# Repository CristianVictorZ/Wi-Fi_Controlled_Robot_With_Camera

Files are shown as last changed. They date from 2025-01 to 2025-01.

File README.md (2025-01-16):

# Wi-Fi Controlled Robot With Camera

## Introduction

  The project is a spider with 4 legs controlled through Wi-Fi. It is equiped with a camera that will transmit the images it records to the app that controls it.

## Description

  The spider will use an ESP32 microcontroller for its access to Wi-Fi. The ESP32 will be connected through I2C to a Camera Module with a FIFO buffer and through serial to another microcontroller, the ESP8266. The ESP8266 will be connected through I2C to a servo motor driver and a gyroscope. The robot will be controlled through an app to which it will transmit the images the camera records. For its power source, 2 18500 Li-ion Batteries will be used. The batteries together supply 7.4V and 4800mAh. As 7.4V is to high for the Servo Driver, a Voltage Step Down Module will be used to reduce it to 5V. A switch is placed between the Batteries and the Voltage Step Down Module to turn off the robot when not in use.
  Each of its legs will have 2 Servo Motors: one at the base rotating on the Z axis, and one rotating on the X axis.
  The body and the legs of the robot are 3D printed.

## Hardware Design

### Block Diagram

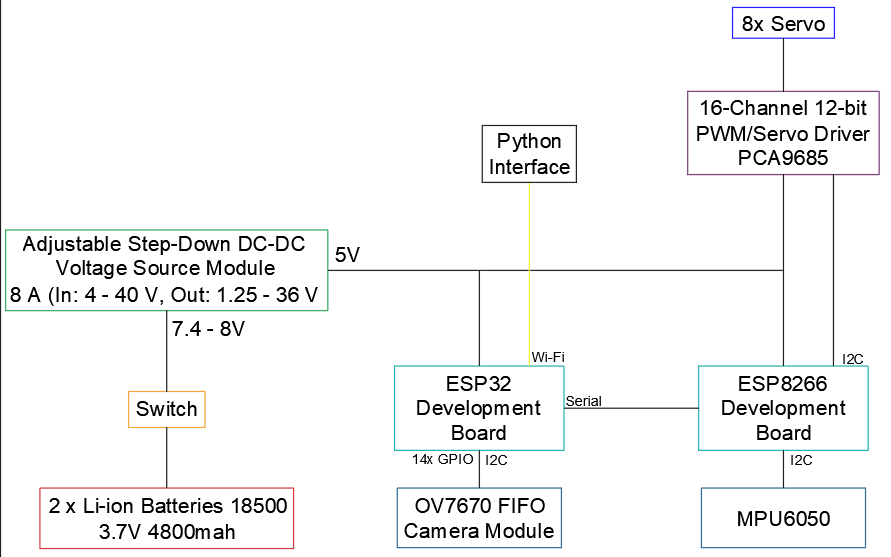
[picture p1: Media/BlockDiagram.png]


### Electric Diagram

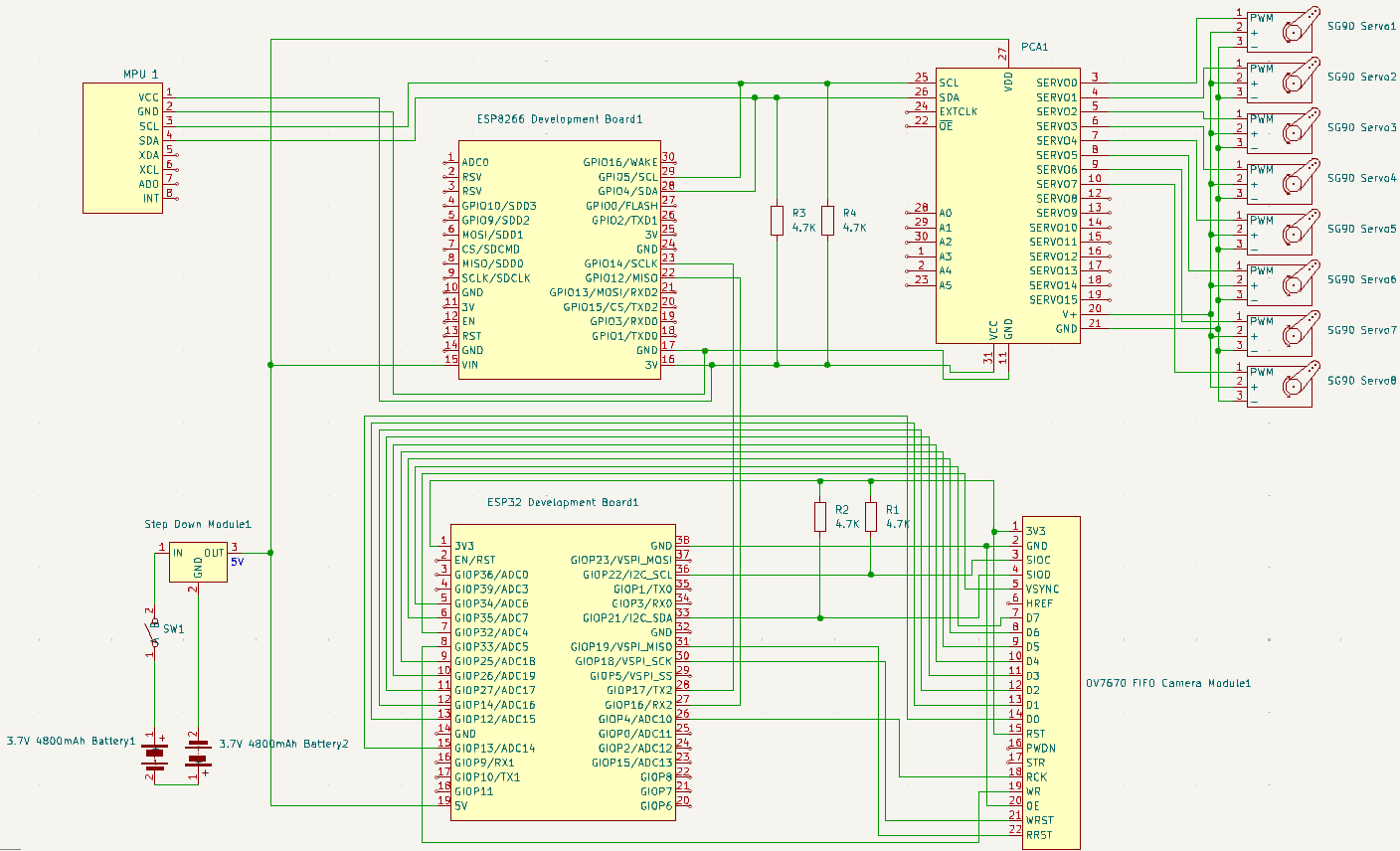
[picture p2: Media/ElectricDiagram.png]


### Components

| Component | Count | Place of Aquisition | Datasheet |
|---|---|---|--- |
| ESP32 Development Board | 1 | Optiums Digital | https://www.espressif.com/sites/default/files/documentation/esp32_datasheet_en.pdf |
| ESP8266 Development Board | 1 | Optimus Digital | https://www.espressif.com/sites/default/files/documentation/esp8266-technical_reference_en.pdf |
| PCA9685 Servo Driver | 1 | Optimus Digital | https://cdn-shop.adafruit.com/datasheets/PCA9685.pdf |
| SG90 Servo Motor | 8 | Optimus Digital | http://www.ee.ic.ac.uk/pcheung/teaching/DE1_EE/stores/sg90_datasheet.pdf |
| OV7670 + AL422B FIFO Camera Module | 1 | Optimus Digital | https://www.haoyuelectronics.com/Attachment/OV7670%20+%20AL422B%28FIFO%29%20Camera%20Module%28V2.0%29/OV7670%20Implementation%20Guide%20%28V1.0%29.pdf|
| Voltage Step Down Module (8A; In: 4-40V, Out: 1.25-36V) | 1 | Optimus Digital | - |
| Battery Support 2x 18500 | 1 | Optimus Digital | - |
| 18500 Li-Ion Battery 3.7V 4800mAh | 2 | - | - |
| 4.7K Resistor | 4 | - | - |
| Wires | - | Optimus Digital | - |

### 3D Model

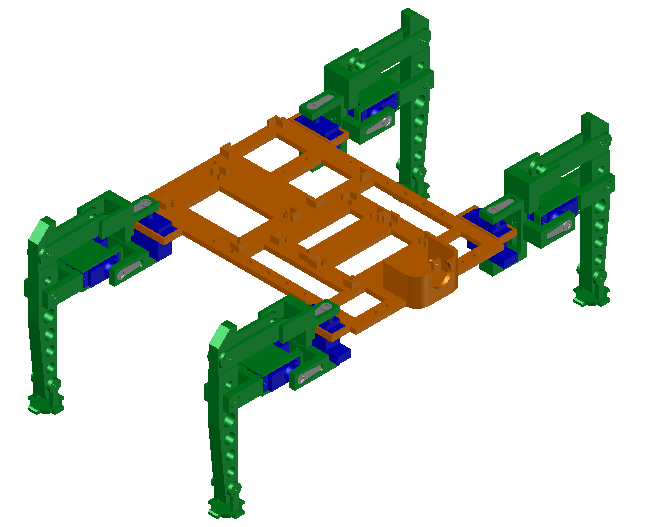
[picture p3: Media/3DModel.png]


### Implementation

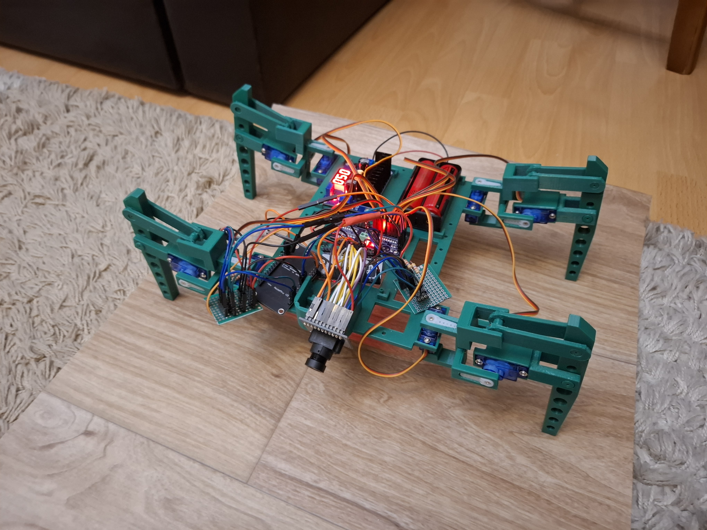
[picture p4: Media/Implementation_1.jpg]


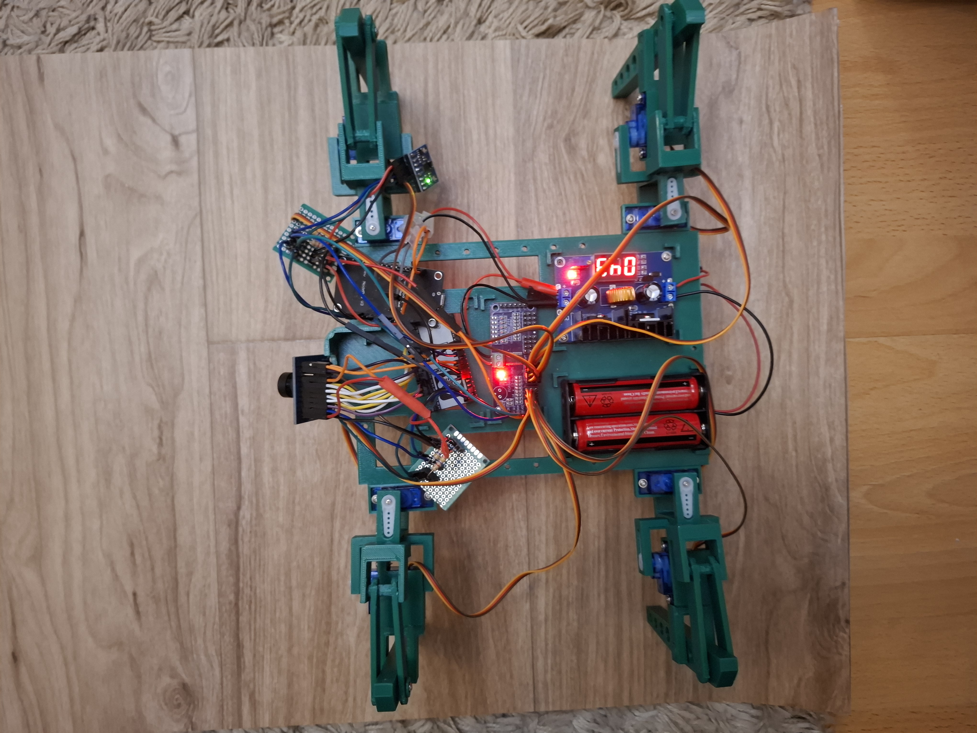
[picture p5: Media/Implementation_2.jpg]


## Software Design

  The software of the robot can be broken into 2 parts: the control of the robot and the interface. The control can also be broken into 3 parts: the wi-fi control, the camera control and the movement control.

  ### Wi-Fi Control

  Wi-Fi is handled by the Core1 on the ESP32. The ESP32 functions as an access point that a client can connect to. It will check in the loop function wether or not a client has connected. Once a client connects, it will begin checking for received messages. When a message is received, it will read the first byte of the message, which identifies the type of message received. The types of messages it can receive from the client are: control update, acknowledge and disconnect. If the message was a control update, it will read the next 3 bytes which represent the 3 variables that coordonate the behaviour of the entire robot: CAMERA_CONTROL1, CAMERA_CONTROL2, MOVEMENT_CONTROL. It will then update its control variables with the ones received and send a confirmation to the client. If the message was an acknowledge, then it means the client confirmed data sent by the Core0, so it will update the variable 'acknowledeAvailable' to let Core0 know it can send the next data set. If the message was a disconnect, the ESP disconnect from the client and resets it's control variables.

  Besides controlling the Wi-Fi, Core1 also handles communication with the ESP8266 through Serial2. When MOVEMENT_CONTROL is updated, it will send through Serial2 the updated variable to the ESP8266.

  ### Camera Control

  The camera is handled by the Core0 on the ESP32. The OV7670 Camera is initialised in the setup function of the program, but afterwards it is controlled only by Core0. It will continuasly check CAMERA_CONTROL1 and CAMERA_CONTROL2 to see if the settings of the camera have to be reconfigured, and if the camera has been enabled. If the camera is enabled it will begin to read and send the frame.

  As stated previosly, the camera has a FIFO memory attached to it. As such, when the camera captures a frame, it will be stored entirely on the FIFO memory, so it is not necessary to store it in a variable. The camera can take pictures in 3 resolutions: 320x240, 160x120, 80x60. Pictures are taken in the RGB565 format: a pixel takes up only 2 bytes, with the first 5 bits being red, the next 6 being green, and the last 5 blue. For easier transmission through Wi-Fi, a variable will store 1024 bytes (+ 1 byte in the begging to indicate the begginig of the set), which will then be sent. Before sending another set of bytes, Core1 will wait for the variable 'acknowledgeAvailable' to indicate that the byte set has been received by the client. If a short amount of time passes with no acknowledge, then the image will no longer be read, and the camera will deactivate.

  ### Other notes regarding the ESP32

  Since both cores can send data thorugh Wi-Fi, the ESP32 uses the mutex library to lock the function for sending data when one of the cores is using it.

  ### Movement Control

  Movement is handled by the ESP8266. It stores 4 matrices that hold the values for each of the 8 motors during a certain movement and an array for idle, that stores the default value for the motors. The 5 matrices are for: forward, backwartd, turn left, turn right. It also stores an array for error values, since the motors are not centered (my bad). It uses the Adafruit Servo Driver to interract with the PCA9685. It will check in its loop for updates to the MOVEMENT_CONTROL variable thorugh a serial port created using the Software Serial library. Depending on its value it will begin one of the movements described. The ESP8266 is also connected to a MPU6050 Accelerometer used to determine the tilt of the body. Based on this, if configured to do so from the interface, it can calculate the error of the servomotrs, and, using a pid, adjust itself so that the body is parallel to the ground.

  ### Interface

  The interface through which the robot is controlled has been realized in Python. The interface uses 3 threads to manage the tasks requiered for controlling the robot.

  The first thread is for the Wi-Fi Control. It uses 2 global variables: a stack for data it receives on Wi-Fi and a stack for data it has to send thorugh Wi-Fi. When it reads data from the Wi-Fi, it is stored in a buffer that can contrain multiple messages appended to each other. Similarly to the ESP32, it checks received data by looking at the first byte of the message. A message can either be a confirmation, or a set of bytes from an image. If it's the former, then the thread will remember it in a variable, and it will remove one byte from the data received buffer. If it's the latter, it will copy the set of bytes to the received data stack and remove 1025 from the data received buffer. If it is neither, then it will begin discarding bytes until it finds a byte that corresponds to one of the previosly mentioned cases. It will repeat this until the buffer is empty. If either thread needs to send data, it will store in the data to send stack, which will be continuasly checked by this thread. After sending a message it will wait for confirmation from the ESP.

  The second thread handles image processing. It receives from the previous thread a set of bytes through the received data stack. It the processes those bytes: it converts them from RGB565 to RGBA and stores it in an array. After receiving a set of bytes, it adds an acknowledge to the data to send stack. Once all of the bytes of an image have been read, it reshapes the array to the correct form, flips it 90 degrees (for some reason the camera just send flipped images; no clue why), converts into an image using the Pillow library and stores it on the computer. It will then change a variable to inform the interface thread to update the image.

  The third thread is the one that generates the actual interface. It uses the PySimpleGUI library to generate it. The interface has its top side the image recorded by the camera, and in the bottom the controls. The controls are a series of checkboxes and radios, for: turning the camera on/off, selecting saturation, brightness and contrast of the camera, turing movement on/off, selecting the movement performed. When a value is changed, it will modify the control variables and add them to the data to send stack. At the very bottom of the interface is an exit button, that when pressed exits the interface (who would have guesses) and adds a value to the data to send stack to announce the ESP32 that the client disconnected.

  ### Other notes

  Initially, both ESPs where going to be programmed in PlatformIO, but after encountering a very persistent error regarding it's flash, the ESP32 was programmed in the Arduino IDE. The Python interface was realized in Spyder.

  The 2 boards are connected to each other through serial interface. The ESP32 uses Serial2 and the ESP8266 uses a serial interface configured with the Software Serial library.
  
## Results

  The robot is cabable of moving, but, because of the motors used, which are rather small, it can struggle a bit. Also, the 3D printed parts are very smooth, and, as such it tends to slip. As for the camera, it can capture and send images, but is rather slow to sending them, and they can come out blurry. Adding a filter for the images on the interface could help with that. Lastly, the 2 batteries get drained rather quickly.

  ### Demo

  Movement Demo
  [](https://youtu.be/AlUA33SjM_I)

  Position Adjustment Demo
  [](https://youtu.be/-0r1mqjBCTA)

  Interface Image Capture Demo
  [](https://youtu.be/xYw6o7V557I)

  | Real Image | Camera Taken Image |
  | ---------- | ------------------ |
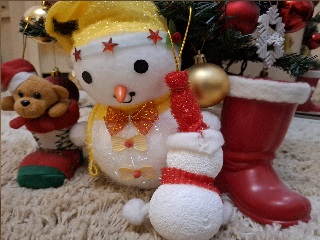
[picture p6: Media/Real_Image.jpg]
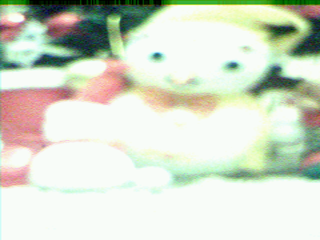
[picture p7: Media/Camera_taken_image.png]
  |  |  |

## Conclusions

  For the first time building something like this, I'm quite satisfied with it. During it's creation, I have learned a lot more about the domain of robotics: about the boards and how they communicate with sensors and each other, about configuring various components, and, most importatnly, that I should probably learn some more mechanics before building something like this again, because I definitely underestimated how much the body would weigh on the legs.
  
  ~~This thing haunts my nightmares.~~

## Resources

  For the camera:
  - https://www.haoyuelectronics.com/Attachment/OV7670%20+%20AL422B%28FIFO%29%20Camera%20Module%28V2.0%29/OV7670%20Implementation%20Guide%20%28V1.0%29.pdf
  - https://www.play-zone.ch/en/fileuploader/download/download/?d=1&file=custom%2Fupload%2FFile-1402681702.pdf

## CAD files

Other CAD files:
3D Printed Parts/Parts.dwg

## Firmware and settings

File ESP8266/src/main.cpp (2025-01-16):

#include <Arduino.h>
#include <SPI.h>
#include <Wire.h>
#include <Adafruit_PWMServoDriver.h>
#include <Adafruit_MPU6050.h>
#include <Adafruit_Sensor.h>
#include <SoftwareSerial.h>
#include <PID.h>

#define SRX D5
#define STX D6

Adafruit_PWMServoDriver servoDriver;
SoftwareSerial espSerial(SRX, STX);
Adafruit_MPU6050 mpu;
#define PID_KP 0.2
#define PID_KD 0.02
#define PID_KI 0.001

char MOVEMENT_CONTROL = 0b00000001;
#define MOVEMENT_ENABLED 7
#define MOVEMENT_IDLE 6
#define MOVEMENT_SELECT 5
#define MOVEMENT_FORWARD 4
#define MOVEMENT_ROTATION 3
#define MOVEMENT_CORRECTION 2

#define NUM_SERVOS 8
#define SERVO_MIN 200
#define SERVO_MAX 500
const int servoPins[8] = {0, 1, 2, 3, 4, 5, 6, 7};

int forwardSwitch = 0, backwardSwitch = 0, leftSwitch = 0, rightSwitch = 0;

const double timeStep = 1.0 / 5.0;
PID *pitchPid = new PID(PID_KP, PID_KD, PID_KI, timeStep);

//0: min - to its right (facing forward); max - to its left
//1: min - upward; max - downward
//2: same as 0
//3: same as 1
//4: min - to its right (facing backward); max - to its left
//5: min - downward; max - upward
//6: same as 4
//7: same as 5

const int idleValues[NUM_SERVOS] = {350, 350, 350, 350, 350, 350, 350, 350};
const int errorValues[NUM_SERVOS] = {50, -70, -10, -70, 10, 10, -50, 10};
int correctionValues[NUM_SERVOS/2] = {0, 0, 0, 0};
unsigned long lastValueLoad = 0;
#define TEST_VALUES_WAIT 4000
const int testValues[8][NUM_SERVOS] = {{250, 250, 250, 250, 250, 250, 250, 250},
                                      {300, 300, 300, 300, 300, 300, 300, 300},
                                      {350, 350, 350, 350, 350, 350, 350, 350},
                                      {400, 400, 400, 400, 400, 400, 400, 400},
                                      {450, 450, 450, 450, 450, 450, 450, 450},
                                      {400, 400, 400, 400, 400, 400, 400, 400},
                                      {350, 350, 350, 350, 350, 350, 350, 350},
                                      {300, 300, 300, 300, 300, 300, 300, 300}};

#define MOVING_VALUES_WAIT 500
const int movingForwardValues[9][NUM_SERVOS] = {{350, 350, 350, 275, 350, 425, 350, 350},
                                          {350, 350, 275, 275, 425, 425, 350, 350},
                                          {350, 350, 275, 350, 425, 350, 350, 350},
                                          {350, 275, 350, 350, 350, 350, 350, 425},
                                          {275, 275, 425, 350, 275, 350, 425, 425},
                                          {275, 350, 425, 350, 275, 350, 425, 350},
                                          {350, 350, 350, 275, 350, 425, 350, 350},
                                          {425, 350, 275, 275, 425, 425, 275, 350},
                                          {425, 350, 275, 350, 425, 350, 275, 350}};
const int movingBackwardValues[9][NUM_SERVOS] = {{350, 350, 350, 275, 350, 425, 350, 350},
                                          {350, 350, 425, 275, 275, 425, 350, 350},
                                          {350, 350, 425, 350, 275, 350, 350, 350},
                                          {350, 275, 350, 350, 350, 350, 350, 425},
                                          {425, 275, 275, 350, 425, 350, 275, 425},
                                          {425, 350, 275, 350, 425, 350, 275, 350},
                                          {350, 350, 350, 275, 350, 425, 350, 350},
                                          {275, 350, 425, 275, 275, 425, 425, 350},
                                          {275, 350, 425, 350, 275, 350, 425, 350}};

#define ROTATING_VALUES_WAIT 500
const int rotatingLeftValues[6][NUM_SERVOS] = {{350, 350, 350, 275, 350, 425, 350, 350},
                                                {350, 350, 425, 275, 425, 425, 350, 350},
                                                {350, 350, 425, 350, 425, 350, 350, 350},
                                                {350, 275, 425, 350, 425, 350, 350, 425},
                                                {350, 275, 350, 350, 350, 350, 350, 425},
                                                {350, 350, 350, 350, 350, 350, 350, 350}};

const int rotatingRightValues[6][NUM_SERVOS] = {{350, 275, 350, 350, 350, 350, 350, 425},
                                                {275, 275, 350, 350, 350, 350, 275, 425},
                                                {275, 350, 350, 350, 350, 350, 275, 350},
                                                {275, 350, 350, 275, 350, 425, 275, 350},
                                                {350, 350, 350, 275, 350, 425, 350, 350},
                                                {350, 350, 350, 350, 350, 350, 350, 350}};

unsigned long lastDriverUpdate = 0;
#define DRIVER_UPDATE_DELAY 200

void updateServo(const int newValues[NUM_SERVOS])
{
  if(MOVEMENT_CONTROL & (1<<MOVEMENT_CORRECTION))
  {
    Serial.print("DA");
    for(int i=0; i<NUM_SERVOS; i++)
    {
      if(i%2==1)
        servoDriver.setPWM(servoPins[i], 0, newValues[i] + errorValues[i] + correctionValues[i/2]);
      else
        servoDriver.setPWM(servoPins[i], 0, newValues[i] + errorValues[i]);
    }
  }else
    for(int i=0; i<NUM_SERVOS; i++)
    {
      servoDriver.setPWM(servoPins[i], 0, newValues[i] + errorValues[i]);
    }
}

void movementTest()
{
  static int step = 0;

  if(millis() - lastValueLoad > TEST_VALUES_WAIT)
  {
    lastValueLoad = millis();
    updateServo(testValues[step]);
    
    step++;
    if(step % 8 == 0)
      step = 3;
  }
}

void movementIdle()
{
  updateServo(idleValues);
}

void movementForward()
{
  static int step = 0;
  if(forwardSwitch == 2)
    step = 0;

  if(millis() - lastValueLoad > MOVING_VALUES_WAIT)
  {
    lastValueLoad = millis();
    updateServo(movingForwardValues[step]);
    
    step++;
    if(step % 9 == 0)
      step = 3;
  }
}

void movementBackward()
{
  static int step = 0;
  if(backwardSwitch == 2)
    step = 0;

  if(millis() - lastValueLoad > MOVING_VALUES_WAIT)
  {
    lastValueLoad = millis();
    updateServo(movingBackwardValues[step]);
    
    step++;
    if(step % 9 == 0)
      step = 3;
  }
}

void movementRotateLeft()
{
  static int step = 0;
  if(leftSwitch == 2)
    step = 0;

  if(millis() - lastValueLoad > ROTATING_VALUES_WAIT)
  {
    lastValueLoad = millis();
    updateServo(rotatingLeftValues[step]);
    
    step++;
    if(step % 6 == 0)
      step = 0;
  }
}

void movementRotateRight()
{
  static int step = 0;
  if(rightSwitch == 2)
    step = 0;

  if(millis() - lastValueLoad > ROTATING_VALUES_WAIT)
  {
    lastValueLoad = millis();
    updateServo(rotatingRightValues[step]);
    
    step++;
    if(step % 6 == 0)
      step = 0;
  }
}

void setup() {
  Serial.begin(115200);
  espSerial.begin(115200);

  Wire.begin();
  mpu.begin();
  
  servoDriver.begin();
  servoDriver.setPWMFreq(50);

  while(!Serial);
  Serial.println("Setup complete!");

  movementIdle();

  mpu.setAccelerometerRange(MPU6050_RANGE_8_G);
  mpu.setGyroRange(MPU6050_RANGE_2000_DEG);
  mpu.setFilterBandwidth(MPU6050_BAND_5_HZ);
}

double roll = 0.00, pitch = 0.00;

void loop() {

  sensors_event_t a, g, temp;
  
  if(millis() - lastDriverUpdate > DRIVER_UPDATE_DELAY)
  {
    lastDriverUpdate = millis();
    if(MOVEMENT_CONTROL & (1<<MOVEMENT_ENABLED))
    {
      if(MOVEMENT_CONTROL & (1<<MOVEMENT_IDLE))
      {
        movementIdle();
      }else
      {
        if(MOVEMENT_CONTROL & (1<<MOVEMENT_SELECT))
        {
          if(MOVEMENT_CONTROL & (1<<MOVEMENT_FORWARD))
          {
            movementForward();
            forwardSwitch = 1;
          }
          else{
            movementBackward();
            backwardSwitch = 1;
          }
        }else
        {
          if(MOVEMENT_CONTROL & (1<<MOVEMENT_ROTATION))
          {
            movementRotateRight();
            rightSwitch = 1;
          }
          else
          {
            movementRotateLeft();
            leftSwitch = 1;
          }
        }
      }
    }
    mpu.getEvent(&a, &g, &temp);

    roll = (atan2(a.acceleration.y , a.acceleration.z) * 57.3 + 90) * 2.77 + 100;
    pitch = (atan2((- a.acceleration.x) , sqrt(a.acceleration.y * a.acceleration.y + a.acceleration.z * a.acceleration.z)) * 57.3 + 90) * 2.77 + 100;

    Serial.print("Acceleration X: ");
    Serial.print(a.acceleration.x);
    Serial.print(", Y: ");
    Serial.print(a.acceleration.y);
    Serial.print(", Z: ");
    Serial.print(a.acceleration.z);
    Serial.print(" m/s^2");
    Serial.print("; Rotation roll: ");
    Serial.print(roll);
    Serial.print(", pitch: ");
    Serial.println(pitch);

    if(MOVEMENT_CONTROL & (1<<MOVEMENT_CORRECTION))
    {
      Serial.print("DA");
      double error = pitch - 350.0;
      float adjustment = (float)pitchPid->Control(error);
      if(correctionValues[0] > 50)
      {
        MOVEMENT_CONTROL &= !(1<<MOVEMENT_CORRECTION);
        for(int i=0; i<4; i++)
        {
          correctionValues[i] = 0;
        }
      }else if(abs(error) > 5)
      {
        for(int i=0; i<4; i++)
        {
          correctionValues[i] = correctionValues[i] + adjustment;//TO CHECK
          //correctionValues[i] = adjustment;
          Serial.print(correctionValues[i]);
          Serial.print(" ");
        }
      }
    }else
    {
      pitchPid->Reset();
      for(int i=0; i<4; i++)
      {
        correctionValues[i] = 0;
      }
    }
    Serial.println(" ");
  }

  if(espSerial.available())
  {
    if(forwardSwitch == 1)
      forwardSwitch = 2;
    if(backwardSwitch == 1)
      backwardSwitch = 2;
    if(rightSwitch == 1)
      rightSwitch = 2;
    if(leftSwitch == 1)
      leftSwitch = 2;
    char receivedValue = espSerial.read();
    MOVEMENT_CONTROL = receivedValue;
    Serial.println(int(receivedValue));
    for(int i=0; i<2; i++)
      receivedValue = espSerial.read();
    movementIdle();
    lastValueLoad = millis();
  }
}

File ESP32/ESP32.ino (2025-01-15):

#include <Arduino.h>
#include <WiFi.h>
#include <Wire.h>
#include <mutex>
#include <HardwareSerial.h>
#include <camera.h>
#include <fifo.h>

std::mutex wifiMtx;
TaskHandle_t taskCamera;

const char* ssid = "ESP32";
const char* password = "arduino142857";

char CAMERA_CONTROL1, CAMERA_CONTROL2, MOVEMENT_CONTROL;

#define CAMERA_ENABLED 7
#define CAMERA_RESOLUTION1 6
#define CAMERA_RESOLUTION2 5
#define SATURATION_SIGN 4
#define SATURATION_VALUE1 3
#define SATURATION_VALUE2 2

#define BRIGHTNESS_SIGN 7
#define BRIGHTNESS_VALUE1 6
#define BRIGHTNESS_VALUE2 5
#define CONTRAST_SIGN 4
#define CONTRAST_VALUE1 3
#define CONTRAST_VALUE2 2

#define MOVEMENT_ENABLED 7
#define MOVEMENT_IDLE 6
#define MOVEMENT_SELECT 5
#define MOVEMENT_FORWARD 4
#define MOVEMENT_ROTATION 3

#define D0 13
#define D1 12
#define D2 14
#define D3 27
#define D4 26
#define D5 25
#define D6 35
#define D7 34

#define PIXEL_SIZE 2
//volatile int xResolution = 320, yResolution = 240;

#define RECEIVED_ACKNOWLEDGE 6
#define RECEIVED_UPDATE 12
#define RECEIVED_DISCONNECT 255
#define STATUS_CONFIRM 1

#define MAX_BYTES_SEND 1025
#define BYTE_SET_START 0b00010000
char frameByteSet[MAX_BYTES_SEND + 1];
char acknowledeAvailable = 0;

unsigned long startWaitTime;
#define TIME_TO_WAIT_FOR_ANSWER 3000
#define START_DELAY 3000
#define PET_WATCHDOG0_DELAY 1000
#define PET_WATCHDOG0_2_DELAY 10
#define PET_WATCHDOG1_DELAY 20

TaskHandle_t taskImageReadAndSend;

WiFiServer server(10000); 
static WiFiClient client;
boolean alreadyConnected = false;

void send_wifi(const char *_data)
{
  std::lock_guard<std::mutex> lck(wifiMtx);
  client.println(_data);
}

void updateCoreControl(char _con1, char _con2, char _con3)
{
  char lastMovControl = MOVEMENT_CONTROL;
  CAMERA_CONTROL1 = _con1;
  CAMERA_CONTROL2 = _con2;
  MOVEMENT_CONTROL = _con3;
  if(lastMovControl != MOVEMENT_CONTROL)
  {
    Serial2.println(MOVEMENT_CONTROL);
  }
}

unsigned char readByte()
{
  unsigned char b;

  digitalWrite(RCK, 1);

  b = digitalRead(D0) | (digitalRead(D1) << 1) | (digitalRead(D2) << 2) | (digitalRead(D3) << 3) |
      (digitalRead(D4) << 4) | (digitalRead(D5) << 5) | (digitalRead(D6) << 6) | (digitalRead(D7) << 7);

  digitalWrite(RCK, 0);

  return b;
}

void readFrame(int xRes, int yRes, int bytes)
{
  fifoReset();

  int bytesLoaded = 1, messageLength;
  frameByteSet[0] = BYTE_SET_START;
  frameByteSet[MAX_BYTES_SEND] = 0;
  unsigned char fr1, fr2;
  char answer[3];
  for(int y = 0; y<yRes; y++)
  {
    for(int x = 0; x<xRes; x++)
    {
      fr1 = readByte();
      if(fr1 == 0)
        fr1 = 1;
      frameByteSet[bytesLoaded++] = char(fr1);
      fr2 = readByte();
      if(fr2 == 0)
        fr2 = 1;
      frameByteSet[bytesLoaded++] = char(fr2);
      if(bytesLoaded % MAX_BYTES_SEND == 0)
      {
        send_wifi(frameByteSet);
        delay(PET_WATCHDOG0_2_DELAY);
        bytesLoaded = 1;
        startWaitTime = millis();
        while(!acknowledeAvailable && millis() < TIME_TO_WAIT_FOR_ANSWER + startWaitTime);
        if(millis() >= TIME_TO_WAIT_FOR_ANSWER + startWaitTime)
        {
          y = 1000;
          x = 1000;
          Serial.println("Time expired!");
          CAMERA_CONTROL1 &= !(1 << CAMERA_ENABLED);
          client.stop();
        }else
        {
          acknowledeAvailable = 0;
        }
      }
    }
  }
  if(bytesLoaded > 1)
  {
    send_wifi(frameByteSet);
    delay(10);
    startWaitTime = millis();
    while(!acknowledeAvailable && millis() < TIME_TO_WAIT_FOR_ANSWER + startWaitTime);
    if(millis() >= TIME_TO_WAIT_FOR_ANSWER + startWaitTime)
    {
      Serial.println("Time expired!");
      CAMERA_CONTROL1 &= !(1 << CAMERA_ENABLED);
      client.stop();
    }else
    {
      acknowledeAvailable = 0;
    }
  }
}

void captureAndSendFrame()
{
  while(!digitalRead(VSY));
  while(digitalRead(VSY));
  prepareFrameCapture();
  startFrameCapture();
  while(!digitalRead(VSY));
  stopFrameCapture();
  readFrame(xResolution, yResolution, PIXEL_SIZE);
}

void cameraHandler(void *pvParameters)
{
  for(;;)
  {
    if((CAMERA_CONTROL1 & (1 << CAMERA_ENABLED)))
    {
      captureAndSendFrame();
    }
    delay(PET_WATCHDOG0_DELAY);
    
    int cmrRes = (1 & (CAMERA_CONTROL1 >> CAMERA_RESOLUTION1)) + (1 & (CAMERA_CONTROL1 >> CAMERA_RESOLUTION2));
    cameraSetResolution(cmrRes);
    int cmrSat = ((1 & (CAMERA_CONTROL1 >> SATURATION_SIGN)) * (-2) + 1) * ((1 & (CAMERA_CONTROL1 >> SATURATION_VALUE1)) * 2 + (1 & (CAMERA_CONTROL1 >> SATURATION_VALUE2)));
    cameraSetSaturation(cmrSat);
    int cmrBri = ((1 & (CAMERA_CONTROL2 >> BRIGHTNESS_SIGN)) * (-2) + 1) * ((1 & (CAMERA_CONTROL2 >> BRIGHTNESS_VALUE1)) * 2 + (1 & (CAMERA_CONTROL2 >> BRIGHTNESS_VALUE2)));
    cameraSetSaturation(cmrBri);
    int cmrCntr = ((1 & (CAMERA_CONTROL2 >> CONTRAST_SIGN)) * (-2) + 1) * ((1 & (CAMERA_CONTROL2 >> CONTRAST_VALUE1)) * 2 + (1 & (CAMERA_CONTROL2 >> CONTRAST_VALUE2)));
    cameraSetSaturation(cmrCntr);

    delay(PET_WATCHDOG0_DELAY);
  }
}

void setup()
{
  Wire.begin();

  Serial.begin(115200);
  Serial2.begin(115200, SERIAL_8N1, 16, 17);

  pinMode(VSY, INPUT);

  pinMode(RCK, OUTPUT);
  pinMode(WR, OUTPUT);
  pinMode(RRST, OUTPUT);
  pinMode(WRST, OUTPUT);

  digitalWrite(WR, 1);
  digitalWrite(WRST, 1);
  digitalWrite(RRST, 1);

  pinMode(D0, INPUT);
  pinMode(D1, INPUT);
  pinMode(D2, INPUT);
  pinMode(D3, INPUT);
  pinMode(D4, INPUT);
  pinMode(D5, INPUT);
  pinMode(D6, INPUT);
  pinMode(D7, INPUT);

  delay(START_DELAY);
  cameraInit();

  WiFi.softAP(ssid, password);
  IPAddress IP = WiFi.softAPIP();
  Serial.print("AP IP address: ");
  Serial.println(IP);

  server.begin();

  delay(START_DELAY);
  xTaskCreatePinnedToCore(
                    cameraHandler,
                    "TaskCamera",
                    4096,
                    NULL,
                    1,
                    &taskCamera,
                    0);  
}

void loop()
{
  if (!client)
    client = server.available();
  if (client)
  {       
    if (!alreadyConnected)
    {
      client.flush();
      alreadyConnected = true;
    }
    
    int messageLength;
    char receivedData[3], statusMessage[2];

    if(client.available())
    {
      do{
        client.readBytes((char*)&receivedData, sizeof(char));
        if(receivedData[0] == RECEIVED_UPDATE)
        {
          client.readBytes((char*)&receivedData, 3*sizeof(char));
          updateCoreControl(receivedData[0], receivedData[1], receivedData[2]);
          statusMessage[0] = STATUS_CONFIRM;
          statusMessage[1] = 0;
          send_wifi(statusMessage);
        }else if(receivedData[0] == RECEIVED_ACKNOWLEDGE)
        {
          acknowledeAvailable = 1;
        }else if(receivedData[0] == RECEIVED_DISCONNECT)
        {
          client.stop();
          updateCoreControl(0x01, 0x01, 0x01);
        }
      }while(client.available());
    }
  }
  delay(PET_WATCHDOG1_DELAY);
}

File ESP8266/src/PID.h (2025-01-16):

#ifndef PID_H_
#define PID_H_

class PID
{
    private:

    double timeStep = 0;
    double inverseTimeStep = 0;
    double errorSum = 0;
    double lastError = 0;
    bool firstRun = true;

    public:

    double pidKp = 0;
    double pidKi  = 0;
    double pidKd = 0;
    double value;

    PID(double _kp, double _ki, double _kd, double _timeStep)
    {
        pidKp = _kp;
        pidKi = _ki;
        pidKd = _kd;
        timeStep = _timeStep;
        inverseTimeStep = 1 / timeStep;
    }

    double Control(double error)
    {
        double errorDerivative = (error - lastError) * inverseTimeStep;

        if (firstRun)
        {
            errorDerivative = 0;
            firstRun = false;
        }

        errorSum = GetIntegral(error, errorSum, timeStep);

        lastError = error;

        value = pidKp * error + pidKi * errorSum + pidKd * errorDerivative;
        return value;
    }

    double Control(double error, double _timeStep)
    {
        if (_timeStep != timeStep)
        {
            timeStep = _timeStep;
            inverseTimeStep = 1 / timeStep;
        }
        return Control(error);
    }

    void Reset()
    {
        errorSum = 0;
        lastError = 0;
        firstRun = true;
    }

    protected:

    virtual double GetIntegral(double currentError, double errorSum, double timeStep)
    {
        return errorSum + currentError * timeStep;
    }
};

#endif
